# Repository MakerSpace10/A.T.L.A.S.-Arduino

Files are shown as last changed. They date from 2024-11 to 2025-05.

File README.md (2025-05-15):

# A.T.L.A.S.-Arduino

The acronym 'A.T.L.A.S.' stands for 'Aboriginal Traversal Land Analysis System'. I named it this because it is my first real robotics project and it can traverse the land around it.

The goal of this project is to create a two-wheeled, self-balancing robot, that can be remote controlled by a Wii Nunckuck. This project was originally intended for a [competition](https://robogames.net/rules/balancer.php) in the [Robo Games](https://robogames.net/index.php) event, in California. The two main focuses of the project are: the Wii Nunchuck "adapter", and the robot itself. Here is a deep dive into the build process/code. The code examples can be found in their entirety in the folder above.

## Remote

### Library
The Wii Nunchuck uses the I2C protocal to comunicate with the Wii Remote, the Arduino boards also use this to communicate with sensors. If you look on the inside of the Nunchuck plug, the slot there is conviniently the same thickness as a common circut board. This will allow for the use of a [Wii Nunckuck Adapter](https://www.amazon.com/FainWan-Compatible-WiiChuck-Nunchuck-Ar-duino/dp/B09LM69T4V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). For wiring ONLY, follow this [guide](https://www.youtube.com/watch?v=vhJRR_7m6z4). As for programming, user [madhephaestus](https://github.com/madhephaestus) has done the hard part and created a library to communicate with the Wii Nunchuck. This library is called [Wiichuck](https://github.com/madhephaestus/WiiChuck) and has been vetted by Arduino themselves. Please note: the Wii Nunchuck has a joystick, two buttons, a gyroscope/accelerometer; I will only use the joystick. If you want to use the other values, please look through the library documentation.

After adding the library to your IDE, you can get started. Start by using a global variable:
```
Accessory nunchuck1;
```
This is an object that will represent the Nunckuck.

```
nunchuck1.begin(); // Initialize the WiiChuck object
nunchuck1.type = NUNCHUCK;
```
The first line initializes the object. Now it is the Nunckuck object. The library can be used for any Wii accessories. The second line is there to prevent any errors that the library may have regognizing the accessory. 

```
nunchuck1.readData();
Serial.print("X: ");
Serial.println(nunchuck1.getJoyX());
Serial.print("Y: ");
Serial.println(nunchuck1.getJoyY());
```
This takes in the updated values comming from the Wii Nunchuck and prints them to the Serial Monitor. All the functions are very intuitive and self explanitory. The rest of the code is in the "Code/WiichuckStarter" folder.

### Transceiver
A transceiver is a modual that can send and recive data. For this project I used the NRF24L01 base modual. This has a range of about 100 meters. In freedom units that's over 300 feet. When adding it to the project, follow [How to Mechatronics](https://howtomechatronics.com/tutorials/arduino/arduino-wireless-communication-nrf24l01-tutorial/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,-Let's%20take%20a&text=It%20uses%20the%202.4%20GHz,2.4%20%E2%80%93%202.5GHz%20ISM%20band) guide. They go into much further detail than I care to do. When wiring, include a 10-100 uF capasitor. This will prevent any power supply noise and any associated issues.

```
RF24 radio(7, 8); // CE, CSN
```
Setting the radio's pins to specific ones on the board.

```
const byte address[6] = "00001";
```
This is the address of the transceiver. The transceiver will only send to / recive from this address. The prefix "const" just means it can't change.

```
struct Data_Package {
  int joyX = 0;
  int joyY = 0;
};
```
This is the data package that is sent over the transceiver. Think of it like any other package: it has contence and will only be sent to one address. The largest it can be is 32 bytes, this example is 4 bytes, so we're safe.

After the code previosly mentioned, it becomes very different based on what task it's doing. See the [How to Mechatronics](https://howtomechatronics.com/tutorials/arduino/arduino-wireless-communication-nrf24l01-tutorial/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,-Let's%20take%20a&text=It%20uses%20the%202.4%20GHz,2.4%20%E2%80%93%202.5GHz%20ISM%20band) guide for the full explanation.

Both the transceiver and the Nunchuck operate with 3.3v. The Arduino Uno only has one 3.3v pin; plugging both into the same pin would draw too much current (mA). This could damage the board. I found it's better to use the 5v pin and add a voltage regulator before adding the pins for the transeciver and the Nunchuck. This brings the voltage to the needed 3.3v while also making more current (mA) avalible to the curcit. When using a breadboard, select three rows (one for GND, one for input VCC, and one for output VCC). The regulator will connect to all three. Follow it [guide](https://www.youtube.com/watch?v=zMA1PjUn87g) for a visual representation. Remember to add the 10 uF capasitor after the regulator and before the transeciver/Nunchuck. The rest of the code is in the "Code/FinalRemote" and "Code/Receiver" folders.

Don't worry if the cover doesn't sit nicely on the housing. The amount of wires need to make the project function will push the cover off.

When pluging the Nunchuck into the 'adapter', be sure to have the 'dip' of the plug facing up. If an off-brand Nunchuck is used, there may not be proper contanct. I suggest sticking to the ones sold by Nintendo directly. 

## Robot

### Gyroscope
If the robot is going to balace on two wheels, it needs to detect when it is tilting/falling. That is the job of the GY-521 modual. This also uses the I2C protocall to comunicate. We will use the Wire library to do so, because we don't need to do anything fancy. The MPU6050 library will allow for easy reading of the data. 

```
MPU6050 mpu;
```
This creates the object that the code can refer to anywhere.

```
int16_t ax, ay, az;
int16_t gx, gy, gz;
```
This creates a name for all the values provided by the GY-521.

Start the I2C communication with 
```
Wire.begin();
```
and initialize the mpu object with 
```
mpu.initialize();
```

It's always good to test for proper conection. The following detects (and tells you) if everything is properly conected:
```
if (mpu.testConnection()) {
    Serial.println("MPU6050 connection successful");
  } else {
    Serial.println("MPU6050 connection failed");
  }
```

Assign the values to their variable names
```
mpu.getAcceleration(&ax, &ay, &az);
mpu.getRotation(&gx, &gy, &gz);
```

Now print them to the Serial moitor for user readability:
```
// Print accelerometer values (in raw units)
Serial.print("Accelerometer X: ");
Serial.print(ax);
Serial.print(" Y: ");
Serial.print(ay);
Serial.print(" Z: ");
Serial.println(az);

// Print gyroscope values (in raw units)
Serial.print("Gyroscope X: ");
Serial.print(gx);
Serial.print(" Y: ");
Serial.print(gy);
Serial.print(" Z: ");
Serial.println(gz);
```

This explains how to get the raw, non-human readable values of the gyroscope. However to avoid too much complex math, and not confuse ourselves in the process, we stick to the accelerometer values. The number used calculates the value for normal gravity:
```
float Ax = (float)ax / 16384.0;
float Ay = (float)ay / 16384.0;
float Az = (float)az / 16384.0;
```

Calculate the pitch angle:
```
float pitch = atan2(Ax, sqrt(Ay * Ay + Az * Az)) * 180.0 / PI;
```

For sanity's sake, I added a sensor fillter. This will take the average of a specified number of gyroscope values, and prevent the robot from having (its equvilent to) a seizure.
```
int FILTER_SIZE = 10 // Number of readings to average
double pitchReadings[FILTER_SIZE]; // Array to store the last N readings
int currentIndex = 0; // Current index for storing readings
double pitchFiltered = 0; // The filtered pitch value
```

and the filter array to be all 0's:
```
for (int i = 0; i < FILTER_SIZE; i++) {
  pitchReadings[i] = 0;
}
```

The rest of the filter is straight forward:
```
// Remove the oldest reading and add the new pitch reading
pitchReadings[currentIndex] = pitch;
  
// Move to the next index (wrap around if necessary)
currentIndex = (currentIndex + 1) % FILTER_SIZE;

// Calculate the average of the last N readings
pitchFiltered = 0;
for (int i = 0; i < FILTER_SIZE; i++) {
  pitchFiltered += pitchReadings[i];
}
pitchFiltered /= FILTER_SIZE;
// Reduces sudden jumps in sensor readings caused by noise, leading to smoother control of the system.
// This helps the PID controller perform more effectively since it's operating on a less noisy signal.
// In dynamic systems, a filter helps the controller focus on significant changes in the input rather than reacting to minor fluctuations.
```

The rest of the code is in the "Code/Gyro" folder.

### Stepper Motor
In order for the robot to corecct its balance, and move in general: I'm using two NEMA 17 stepper motors. They will provied a good balace of acuracy and weight (so the robot does't fall over). For wiring, follow this [guide](https://www.youtube.com/watch?v=7spK_BkMJys). The video is good for side by side walkthroughs, the [website](https://howtomechatronics.com/tutorials/arduino/stepper-motors-and-arduino-the-ultimate-guide/) is better for self-pacing. Make sure: everything is wired correctly, the driver is set correctly, and that the battery is charged/not weak.

If you're using the wires provided by the seller to connect the motor to the driver, the wire to pin translation is: Black to 1A, Green to 1B, Red to 2A, and Blue to 2B.

I will be using the AccelStepper library to control both motors. Lets start with one:

Define the pins that control the stepper motor:
```
#define stepPin 2
#define dirPin 3
```

Create a stepper motor object (We will refer to this when calling the functions):
```
AccelStepper stepper(AccelStepper::DRIVER, stepPin, dirPin);
```

Set both the max speed and the acceleration of the motor:
```
stepper.setMaxSpeed(1000); // Max speed (steps per second)
stepper.setAcceleration(50); // Acceleration (steps per second^2)
```

You could set the starting position (This is so you can move it by position, instead of times rotated): 
```
stepper.setCurrentPosition(0);
```

Rotate the wheel to position 800:
```
stepper.moveTo(800);
// Run the motor until it reaches the target position
while (stepper.distanceToGo() != 0) {
  stepper.run(); // Keep the motor moving towards the target
}
```

AccelStepper allows for changing the direction to be easy, just use a negative sign (-).
```
stepper.moveTo(-800);
```

The code listed above allows for movement by absolute position, not by steps. Instead the following function is used:
```
stepper.move(800);
```
This will rotate the stepper 4 times (800 steps / 200 steps per rotation = 4 rotations), no matter what position it is at. With this method, the idea of using a negative sign still works the same way. The only difference is now the code does not need to check if the stepper has rotated enough.

However, for this project, I need the speed of the wheels to change, no the steps. In stead I use 
```
stepper.setSpeed(800);
```
The idea of the negative sign changing directions still works here. At the beginning of the loop, add
```
stepperR.runSpeed();
```
as the steppers need to run continuously.

The rest of the code (and use of the two different functions) is in the "Code/Stepper" folder.

### Balancing
For the robot to balance on it's own: it needs a special controller called a P.I.D. Controller. P.I.D. stands for Proportional-Integral-Derivative. There is a lot of complicated math to it. To put it Layman's terms: it takes the angle we are leaning at, compares it to the angle we want to be at (0 degrees for straight up), to find out how drasticly we need to move to get there and not fall over. Use these guides: [Hackster.io](https://www.hackster.io/marketingmanagerofdattabanur/arduino-self-balancing-robot-e23f9c), [What is a P.I.D. Control](https://www.youtube.com/watch?v=wkfEZmsQqiA), [PID Control - A brief introduction](https://www.youtube.com/watch?v=UR0hOmjaHp0), and the PID Explaination PDF to understand the concepts better. Each robot will be built differently, so the P.I.D. variables will need to be tweaked. The general ideas will always be present.

The P.I.D. library in this example is the [PID_v1](https://github.com/br3ttb/Arduino-PID-Library/tree/master). I found it to be simple and easy to use. Please note that you need to manually download the library from the repository, and upload it to the Arduino IDE. 

The import statment needs to look like this:
```
#include <PID_v1.h>
```

Now set all variables the P.I.D. controller uses:
```
double Setpoint, Input, Output;
double Kp = 2.0, Ki = 5.0, Kd = 1.0;
PID myPID(&Input, &Output, &Setpoint, Kp, Ki, Kd, DIRECT);
```

Set the P.I.D. controller values:
```
Setpoint = 0; // Target angle (e.g., 0 degrees pitch)
myPID.SetMode(AUTOMATIC);
```

Outside both loops, to insure consistancy with the P.I.D., I added 
```
unsigned long lastPIDTime = 0;
const unsigned long pidInterval = 10; // PID update interval in ms
```
This controlls how often the controller updates. 

With this we can set the input for the P.I.D. controller to the output of the sensor filter:
```
// Set the input value for the PID control (filtered sensor data)
Input = -1 * abs(pitchFiltered);
```
The controller doesn't seem to respond well with positive values, so I just made them all negative

However: there mayby some margin of error (with the electronics or the way the robot was built), the angle might be off slightly.
To fix this: once the robot is built, stand it to be as straight up as possible. Take the angle that appears after filtering and add/subtract as needed.
Just the number before the decimal point will do. Ex.: if the robot is standing straight up and the angle is -3:
```
pitchFiltered += 3;
```
This is needed before use anywhere else. The line before setting the value of "Input" is ideal.

With that all set, we can run the P.I.D. controller:
```
myPID.Compute();
```
It's as simple as that. This will automaticly set the value of 'Output', which will be used to change the stepper motor behavior.
When it comes to controlling the stepper motors with "Output", the value does not translate perfectly to motor steps, so we multiply.

This way the stepper motors will move the appropiate amount of steps to remain upright. It will move the appropiate direction based of of the direction of the pitch.

As a neat feature (for sanity's sake), it's good to stop the robot from moving if it leans too much. After the pitch passes a certain threshold, it cannot prevent itself from falling over. If it does, the wheels will keep spining, continuing to move the robot. To avoid this, "Input" is set inside a if statment:
```
// A max of 15 degree tilt
if(abs(pitchFiltered) < 15){
  Input = -1 * abs(pitchFiltered);
  myPID.Compute();

  stepSpeed = (int)(Output * 10);
  if(pitchFiltered > 0){
    stepper.setSpeed(stepSpeed);
  }else{
    stepper.setSpeed(-stepSpeed);
  }
}else{
  Serial.println("Please reset robot position.");
  stepper.setSpeed(0);
}
```

For debugging (optional):
```
Serial.print("Pitch: ");
Serial.print(pitchFiltered);
Serial.print("\tOutput: ");
Serial.print(Output);
Serial.print("\tError: ");
Serial.print(Setpoint - pitchFiltered);
Serial.print("\tSpeed: ");
Serial.println(stepSpeed);
```

Finnally, the reciver and the balancer code combine. The balancer code will take priority, so the robot doesn't fall over.

### Remote Commands
The Nunchuck values will not be (0,0) at the center. All values will vary slightly, reguardless of previous recorded positions. So to overcome this, create a board representing the positions of the joy stick on the Nunchuck, and note the values. I decided to constrain the values of 'x' and 'y' for later use:
```
  //                              Left, Right
  int x = (int)constrain(data.joyX, 30, 225);
  //                              Back, Forth
  int y = (int)constrain(data.joyY, 40, 230);
```

To prevent the robot from moving when the joy stick is in the center, I created the controls to be around a range of values. This creates a "hole" of values, to which the robot will not respond to. Please note that these are the values I got and guessed; it will be different for you. The following is a rough idea on interpreting the Nunchuck data:
```
//Left then Right
int turnSpeed;
if(x <= 125){
  turnSpeed = (int)map(x, 30, 125, 5, 50);
  stepperR.setSpeed(turnSpeed);
  stepperL.setSpeed(turnSpeed);
}else if(x >= 135){
  turnSpeed = (int)map(x, 135, 230, 5, 50);
  stepperR.setSpeed(-turnSpeed);
  stepperL.setSpeed(-turnSpeed);
}
Serial.print("\t X speed: ");
Serial.print(turnSpeed);
//Back then Forward
int linSpeed;
if(y <= 135){ 
  linSpeed = (int)map(y, 40, 135, 5, 100);
  stepperR.setSpeed(-linSpeed);
  stepperL.setSpeed(linSpeed);
}else if(y >= 145){
  linSpeed = (int)map(y, 145, 225, 5, 100);
  stepperR.setSpeed(linSpeed);
  stepperL.setSpeed(-linSpeed);
}
Serial.print("\t Y speed: ");
Serial.println(linSpeed);
```

Turning is the most unstable, so it will be slower comparded to forward and back. To turn properly, the motors need to move in opposite directions; because they face the opposite way physically, we give them the same command. Moving back/forth is straight-forward.

Warning: before using any of the code mentioned abouve, remove any and all delays and make sure all values match YOUR setup, or the code will note work the way it should. 

Happy Trails!

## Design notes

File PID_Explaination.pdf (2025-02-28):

# PID Controller

PID stands for Proportional-Integral-Derivative, and it’s a type of control algorithm used to help systems reach a desired goal or setpoint (like keeping the temperature of a room constant).
Here’s a simple breakdown of the three components of a PID controller:
1. Proportional (P):
This part looks at the current error, which is how far the system is from the target value. The proportional part tries to correct the error by applying a correction that’s proportional to the size of the error.
Example: If your room is 5°C cooler than desired, the system will apply a correction that's proportional to that error (say, 5 times some constant).
2. Integral (I):
This part looks at the accumulated error over time. If there’s been a small error for a long time, the integral part will work to correct it by adding up all the past errors. This helps eliminate any steady-state errors that the proportional part might miss.
Example: If the room temperature has been slightly too low for a long time, the integral part will push harder to correct this over time.
3. Derivative (D):
This part looks at the rate of change of the error. It anticipates how fast the error is changing and tries to adjust the correction to prevent overshooting or instability.

Example: If the temperature is rapidly increasing towards the target, the derivative part will slow down the heating to avoid going past the target temperature.

### Putting it all together:

A PID controller adjusts the system's output by combining the three components: The Proportional part responds to how big the error is right now.

PID Controller | 1

The Integral part compensates for past errors.

The Derivative part anticipates future changes.
By balancing these three components, the PID controller tries to minimize the error and make the system as stable as possible.

When tuning a PID controller, it’s helpful to understand how each of the three constants (Kp, Ki, and Kd) affects the system behavior. Here's how you can figure out which value to adjust:

### 1. Proportional (Kp) – Adjusting for the Size of the Error

The proportional term determines how much correction is applied based on the current error (the difference between your setpoint and the current value).

If Kp is too high:
The system will respond quickly, but it might overshoot the setpoint, causing the system to oscillate back and forth around the target.

It might cause the system to be "too aggressive," trying to correct too much.

If Kp is too low:
The system will respond too slowly or may never reach the setpoint. It won't be able to overcome the error, and the response will be sluggish.

To adjust Kp:
Start with a small value and increase it gradually.

The goal is to make the system respond quickly to error, but without causing too much overshoot or oscillation.

### 2. Integral (Ki) – Adjusting for Accumulated Error

The integral term accounts for the sum of past errors. This helps the system eliminate steady-state errors (errors that don’t go away with just the proportional term, like if the system stays a little off target over time).
If Ki is too high:

The system might "overcompensate" by continually adding up past errors and trying to correct them too much. This can lead to oscillation or instability.

If Ki is too low:
The system might not be able to eliminate small errors over time, and it might leave a persistent error even after the system seems stable.

To adjust Ki:
Increase Ki slightly if the system is unable to reach the setpoint or if there’s a persistent small error over time.

Reduce Ki if the system becomes unstable or oscillates after reaching the setpoint.

### 3. Derivative (Kd) – Adjusting for Rate of Change

The derivative term looks at how fast the error is changing. It tries to anticipate how the error will evolve and dampens any sudden changes to prevent overshooting.
If Kd is too high:

The system might become overly sensitive to small fluctuations in error, making it too slow or too "nervous," correcting even small changes too much.
If Kd is too low:

The system might overshoot and oscillate because it’s not responding to rapid changes in the error.

To adjust Kd:
Increase Kd if the system is overshooting (going past the setpoint) or if it’s oscillating.

If the system is responding too slowly, try lowering Kd to reduce unnecessary dampening.

### A Practical Process for Tuning:

1. Start with Kp first:

Set Ki and Kd to zero initially.
Gradually increase Kp until the system starts to respond to the error. Look for a value where the system reacts quickly without oscillating too much.
2. Add Ki:
Once Kp is set, start increasing Ki gradually.

If there’s a persistent error (like the system never quite reaches the setpoint), increase Ki to eliminate it.

Be careful not to set Ki too high, as it can cause instability.
3. Add Kd:

Finally, adjust Kd to reduce oscillations and overshooting.
If the system is overshooting or oscillating, increase Kd to help "dampen" the response.

### A Tuning Strategy to Try:

There’s a common strategy called the Ziegler-Nichols Method that can help guide you through the process of tuning PID constants:

1. Set Ki and Kd to 0.
2. Increase Kp until the system starts oscillating.
3. Record the value of Kp at which the system starts oscillating. This is called the ultimate gain (Ku).
4. Measure the period of oscillation, which is the time it takes for one full cycle of oscillation (the ultimate period, Pu).
5. Use the following rules to calculate your PID values:

Proportional (Kp):
Kp=0.6×KuKp = 0.6 \times Ku
Integral (Ki):
Ki=2×Kp/PuKi = 2 \times Kp / Pu

Derivative (Kd):
Kd=Kp×Pu/8Kd = Kp \times Pu / 8

After applying these values, fine-tune them manually for the best performance.

### Other Tips:

Fine-tuning is key. You’ll likely need to tweak the values slightly after using the Ziegler-Nichols method or your initial guesswork.
Monitor system behavior carefully (e.g., through serial prints or graphs) to make sure you're not causing instability.

For very slow systems (like temperature control), a high Ki value is often useful, while for fast-reacting systems (like motors or robots), you might rely more on the proportional and derivative components.

### Example Process:

Let's say you’re controlling a heater's temperature:
1. Set Ki and Kd to 0.
2. Slowly increase Kp until you notice the temperature starts to increase faster but doesn’t oscillate too wildly.
3. If the temperature overshoots and oscillates, add a small Kd to dampen the response.
4. If there's still a persistent low error, slowly increase Ki to help the system get to the target temperature more precisely.

By adjusting these three constants gradually, you can find a balance where the system is stable, responsive, and accurate.

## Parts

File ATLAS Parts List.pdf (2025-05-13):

Remote:
Part Name: | Price - Units: Some links:
Wii Nunchuck | | Make sure that the seller is Nintendo
Arduino Nunchuck Adapter | $13 for 5 | https://www.amazon.com/FainWan-Compatible-WiiChuck-Nunchuck-Ar-duino/dp/B09LM69T4V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 (https://www.amazon.com/FainWan-Compatible-WiiChuck-Nunchuck-Ar-duino/dp/B09LM69T4V?s=videogames)

Arduino Uno/nano
Battery “Pack” | A 9v battery should work fine.
NRF24L01 | $8 -4 | https://www.amazon.com/HiLetgo-NRF24L01-Wireless-Transceiver-Module/dp/B00LX47OCY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 A5HF046HN5ZZYK&psc=1 (https://www.amazon.com/HiLetgo-NRF24L01-Wireless-Transceiver-Module/dp/B00LX47OCY)
10 uF Capacitor | need 2
3.3v Voltage
regulator
| $8 - 20 | https://www.amazon.com/Ferwooh-AMS1117-3-3-4-5V- 7V-AMS1117-3-3V-Converter/dp/B0D17N8WWJ/ref=sr _1_5?crid=26I050O33AR7Y&dib=eyJ2IjoiMSJ9.yYoap YX0zQQVL-GhrZ4MBW5fwuoTvOJPqwwwicoQy3tW pLhC7DvnTZpdporOD4W-J1sqX_HDa0aT5zoH6hzlbvg uVB_GJ-Lvw-RSH27blJZRefK2SKfLUocBsBrzznpvsV q9Ug12vn2sIzaQEEpmxCYL1oHuYf2rWTOw5LPDTp M2epp-RwoUdLc1iKdejKdiajcoiga38SGo1UPzXbp40L ogGkZJbVWgB4BXRnFWGFaDx5gF0UC3OC2LrWiB KNW-Z4qeOSYyR6TuqTqDQt9KvmWsQcyg20MPVpL zhIbBigg.XxFXhx4V4o8Xa2L5BvKZuC0R84E-zATMQ oEUQHv6Z14&dib_tag=se&keywords=5v+to+3.3v+volt age+divider&qid=1747142222&s=industrial&sprefix=5v +to+3.3v+voltage+divider%2Cindustrial%2C57&sr=1-5 (https://www.amazon.com/Ferwooh-AMS1117-3-3-4-5V-7V-AMS1117-3-3V-Converter/dp/B0D17N8WWJ?s=industrial)

Robot:
Part Name: | Price: | Some Links:

Arduino Uno/Nano
2 Stepper Motors | $8-1 or $40 - 5 | https://www.amazon.com/Usongshine-Nema17-Stepper-17HS4401S-Printer/dp/B0787BQ4WH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 (https://www.amazon.com/Usongshine-Nema17-Stepper-17HS4401S-Printer/dp/B0787BQ4WH)

| | q7sbz&content-id=amzn1.sym.a089f039-4dde-401a-9041 -8b534ae99e65&pf_rd_p=a089f039-4dde-401a-9041-8b5 34ae99e65&pf_rd_r=B8Z8AJ2SPGXADPE419P9&pd_r d_wg=vq1IF&pd_rd_r=93860624-13ea-4a1d-8257-0d5a9 e81c6ce&pd_rd_i=B07KW7F3P9&th=1 (https://www.amazon.com/Usongshine-Nema17-Stepper-17HS4401S-Printer/dp/B0787BQ4WH)
2 Stepper Motor Drivers | $10-5 | https://www.amazon.com/HiLetgo-Stepstick-Stepper-Printer-Compatible/dp/B07BND65C8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 07BND65C8&psc=1 (https://www.amazon.com/HiLetgo-Stepstick-Stepper-Printer-Compatible/dp/B07BND65C8)
Stepper Motor Mounting Brackets | $10 - 2 | https://www.amazon.com/weideer-Stepper-Mounting-Bracket-K-029-42/dp/B09372B2D1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 09372B2D1&th=1 (https://www.amazon.com/weideer-Stepper-Mounting-Bracket-K-029-42/dp/B09372B2D1)
GY-521 Accelerometer/Gyro scope | $8.50-3 | https://www.amazon.com/FORIOT-Accelerometer-MPU-6050-Compatible-Converter/dp/B0CDL8DVZ7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 (https://www.amazon.com/FORIOT-Accelerometer-MPU-6050-Compatible-Converter/dp/B0CDL8DVZ7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)
Transceiver | Taken Care of.
Battery Pack | | Find one that the drivers can handle.
100 uF Capacitor | | One for each driver.

### 2 non-slip wheels

and mounting hub

$13-2
and
$14-2

https://www.amazon.com/90-10mm-Black-Robot-Wheels/dp/B00T3MQG7M/ref=sr_1_53?dib=eyJ2IjoiMSJ9.J3dg x8P762UnXWORtlwJYXmVniWD9I0SaMzqaugb5KLU BAPJapvnl7OtTUPSE1LhI3VgLKNvX7wmI0-zaRnMgn GDNnxRQ7D8U_xinsZm4ENyCvHIdXOUPfZb6aoGjUf 6Wge3jFfUSyg81EokhgKNOsa4FpTjyiPosZVvxWJQ09 8sSDo7SOz8R39l0S_avcjpI-lWVV7BhM35hT-ujsWoa-U5dzt3hWNCo6FdP1j1FB1Omf6be6oA0wI54QWy7BL kd_qfB-8SnS2gCqVgXwxTvzH9Q0SlkLZ8sBS4QR2vu 7Q.bxDL5dnFUvPnqkcdF5KDHgBz9bM-7mfJWLQtIcji xac&dib_tag=se&keywords=arduino+wheels&qid=17295 31853&sr=8-53 (https://www.amazon.com/90-10mm-Black-Robot-Wheels/dp/B00T3MQG7M)
and
https://www.amazon.com/Pololu-Universal-Aluminum-MOUNTING-Shaft/dp/B00B887FX8/ref=pd_bxgy_thbs_d_ (https://www.amazon.com/Pololu-Universal-Aluminum-MOUNTING-Shaft/dp/B00B887FX8)

sccl_1/143-0492769-7445039?pd_rd_w=UnJN6&content -id=amzn1.sym.f7fa8b58-6436-47b8-8741-9e90c231669e &pf_rd_p=f7fa8b58-6436-47b8-8741-9e90c231669e&pf _rd_r=3ZPERPRNYQMZRZDAVVQ6&pd_rd_wg=P97 Bp&pd_rd_r=4b8d5db8-37d0-431c-8c29-d2db8ca5031f &pd_rd_i=B00B887FX8&psc=1 (https://www.amazon.com/Pololu-Universal-Aluminum-MOUNTING-Shaft/dp/B00B887FX8)
5mm bars for the
frame
$12-10 | https://www.amazon.com/VictorsHome-Stainless-Crafts- Helicopter-Airplane/dp/B0962X6J95/ref=sr_1_3?crid=3 OTEF9LOTIY3W&dib=eyJ2IjoiMSJ9.ch840XSb-mjD1k YPgweX40GilWj2algdChaO4agcDgWod5fDWyxYlj7SJ 7pQTUngiGWZeF5di4CgiKJmkF2rFuLfFcfKUWopdnG PJ7ohA3ESe980wfDbDK0uust2g1Pjsytb8Qdp6K2e_bnG B2kssx6cMU53DdcFPJF2QCMRpFBUt84RXgI5p6D8h Ox2k8Hf-qbAbDYWbARXy8VGMJUAd2aWMq3STDc 86N3SZKQuCu4.izOUcmmDijLX7o_l7hrYsKBIXQvQ MYoteCUvzMzrgcc&dib_tag=se&keywords=5mm%2Bx %2B200mm%2Brods&qid=1727287311&sprefix=5mm %2Bx%2B200mm%2Brods%2Caps%2C58&sr=8-3&th=
| 1 (https://www.amazon.com/VictorsHome-Stainless-Crafts-Helicopter-Airplane/dp/B0962X6J95)

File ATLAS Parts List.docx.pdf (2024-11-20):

### Remote:

Part Name: | Price: | Some links:

Wii Nunchuck
Arduino Nunchuck Adapter | $13 for 5 | https://www.amazon.com/FainWan-Compatible-WiiChuck-Nunchuck-Ar-duino/dp/B09LM69T4V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 (https://www.amazon.com/FainWan-Compatible-WiiChuck-Nunchuck-Ar-duino/dp/B09LM69T4V?s=videogames)
Logic level shifter | $7.50 - 10 | https://www.amazon.com/HiLetgo-Channels-Converter-Bi-Directional-3-3V-5V/dp/B07F7W91LC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 (https://www.amazon.com/HiLetgo-Channels-Converter-Bi-Directional-3-3V-5V/dp/B07F7W91LC?s=industrial)

Arduino Uno/nano
Battery “Pack” | A 9v battery should work fine.
NRF24L01 | $8 -4 | https://www.amazon.com/HiLetgo-NRF24L01-Wireless-Transceiver-Module/dp/B00LX47OCY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 f&pf_rd_r=HR740JA5HF046HN5ZZYK&psc=1 (https://www.amazon.com/HiLetgo-NRF24L01-Wireless-Transceiver-Module/dp/B00LX47OCY)
10 uF Capacitor | need 2
3.3v Voltage regulator | need 2
3-D printed Housing

### Balancing Robot:

Part Name: | Price: | Some Links:

Arduino Uno/Nano
2 Stepper Motors | $11-1 | https://www.amazon.com/Usongshine-Nema17-Stepper-17HS4401S-Printer/dp/B0787BQ4WH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 pd_rd_i=B07KW7F3P9&th=1 (https://www.amazon.com/Usongshine-Nema17-Stepper-17HS4401S-Printer/dp/B0787BQ4WH)
2 Stepper Motor Drivers | $10-5 | https://www.amazon.com/HiLetgo-Stepstick-Stepper-Printer-Compatible/dp/B07BND65C8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 (https://www.amazon.com/HiLetgo-Stepstick-Stepper-Printer-Compatible/dp/B07BND65C8)

| | .sym.2b132e63-5dcd-4ba1-be9f-9e044543d59f&pf_rd_p= 2b132e63-5dcd-4ba1-be9f-9e044543d59f&pf_rd_r=0BF9X HJZB9Q1QV2H1FRA&pd_rd_wg=u2m9L&pd_rd_r=90a0f3 48-26f9-4319-8482-a2a2ec24d3f9&pd_rd_i=B07BND65C8 &psc=1 (https://www.amazon.com/HiLetgo-Stepstick-Stepper-Printer-Compatible/dp/B07BND65C8)
Stepper Motor Mounting Brackets | $10 - 2 | https://www.amazon.com/weideer-Stepper-Mounting-Bracket-K-029-42/dp/B09372B2D1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 th=1 (https://www.amazon.com/weideer-Stepper-Mounting-Bracket-K-029-42/dp/B09372B2D1)
GY-521 Accelerometer/Gyrosco pe | $8.50-3 | https://www.amazon.com/FORIOT-Accelerometer-MPU-6050-Compatible-Converter/dp/B0CDL8DVZ7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 (https://www.amazon.com/FORIOT-Accelerometer-MPU-6050-Compatible-Converter/dp/B0CDL8DVZ7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)
Transceiver | Taken Care of.
Battery Pack

### 2 non-slip wheels and

mounting hub

$13-2
and
$14-2

https://www.amazon.com/90-10mm-Black-Robot-Wheels/dp/B00T3MQG7M/ref=sr_1_53?dib=eyJ2IjoiMSJ9.J3dgx8P 762UnXWORtlwJYXmVniWD9I0SaMzqaugb5KLUBAPJapvnl 7OtTUPSE1LhI3VgLKNvX7wmI0-zaRnMgnGDNnxRQ7D8U_ xinsZm4ENyCvHIdXOUPfZb6aoGjUf6Wge3jFfUSyg81Eokhg KNOsa4FpTjyiPosZVvxWJQ098sSDo7SOz8R39l0S_avcjpI-l WVV7BhM35hT-ujsWoa-U5dzt3hWNCo6FdP1j1FB1Omf6b e6oA0wI54QWy7BLkd_qfB-8SnS2gCqVgXwxTvzH9Q0SlkLZ 8sBS4QR2vu7Q.bxDL5dnFUvPnqkcdF5KDHgBz9bM-7mfJW LQtIcjixac&dib_tag=se&keywords=arduino+wheels&qid=1 729531853&sr=8-53 (https://www.amazon.com/90-10mm-Black-Robot-Wheels/dp/B00T3MQG7M)
and
https://www.amazon.com/Pololu-Universal-Aluminum-MOUNTING-Shaft/dp/B00B887FX8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 887FX8&psc=1 (https://www.amazon.com/Pololu-Universal-Aluminum-MOUNTING-Shaft/dp/B00B887FX8)
Frame | $12-10 | https://www.amazon.com/VictorsHome-Stainless-Crafts-H elicopter-Airplane/dp/B0962X6J95/ref=sr_1_3?crid=3OTE F9LOTIY3W&dib=eyJ2IjoiMSJ9.ch840XSb-mjD1kYPgweX40 GilWj2algdChaO4agcDgWod5fDWyxYlj7SJ7pQTUngiGWZe F5di4CgiKJmkF2rFuLfFcfKUWopdnGPJ7ohA3ESe980wfDbD K0uust2g1Pjsytb8Qdp6K2e_bnGB2kssx6cMU53DdcFPJF2Q CMRpFBUt84RXgI5p6D8hOx2k8Hf-qbAbDYWbARXy8VGMJ (https://www.amazon.com/VictorsHome-Stainless-Crafts-Helicopter-Airplane/dp/B0962X6J95)

UAd2aWMq3STDc86N3SZKQuCu4.izOUcmmDijLX7o_l7hrY sKBIXQvQMYoteCUvzMzrgcc&dib_tag=se&keywords=5mm %2Bx%2B200mm%2Brods&qid=1727287311&sprefix=5m m%2Bx%2B200mm%2Brods%2Caps%2C58&sr=8-3&th=1 (https://www.amazon.com/VictorsHome-Stainless-Crafts-Helicopter-Airplane/dp/B0962X6J95)

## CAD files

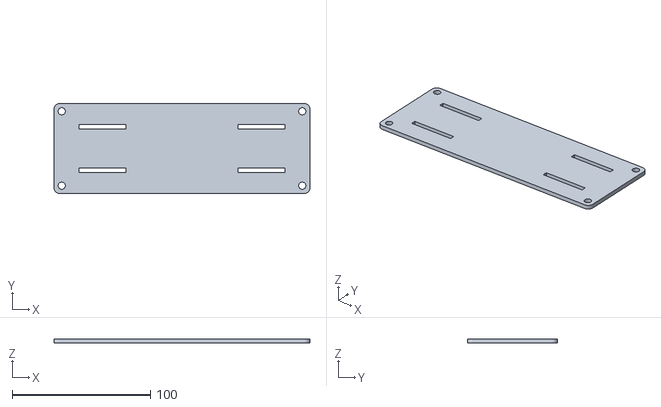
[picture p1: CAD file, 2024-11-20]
STL File/Motor Board.stl
185.0 x 65.0 x 3.00

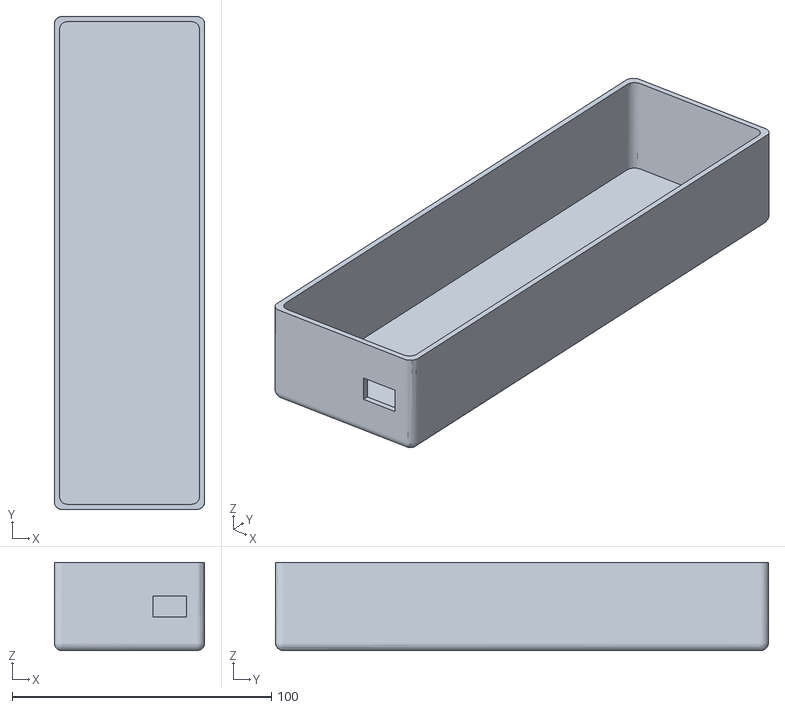
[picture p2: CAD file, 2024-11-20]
STL File/Remote Case.stl
58.0 x 190.0 x 34.0

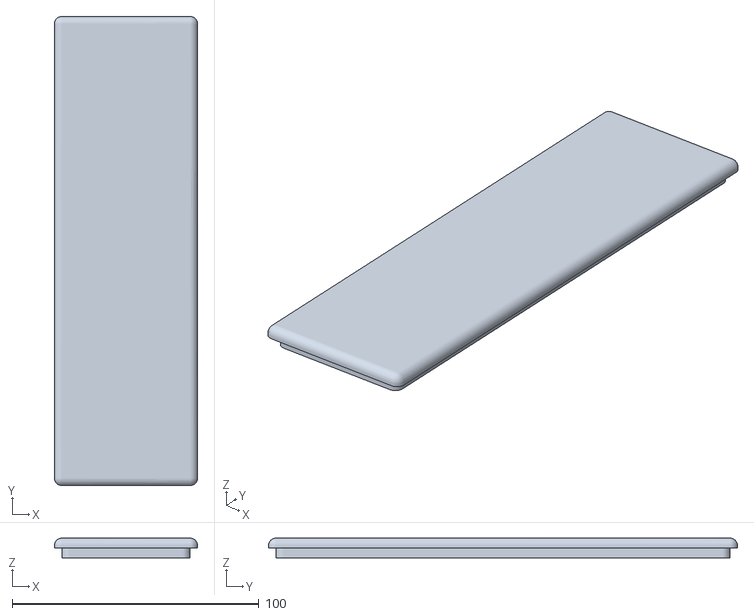
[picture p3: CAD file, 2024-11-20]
STL File/Remote Cover.stl
58.0 x 190.0 x 8.00

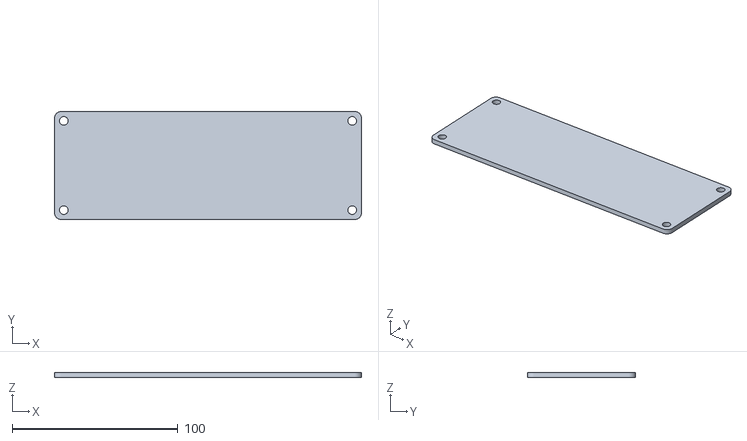
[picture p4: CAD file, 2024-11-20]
STL File/Body Board.stl
185.0 x 65.0 x 3.00

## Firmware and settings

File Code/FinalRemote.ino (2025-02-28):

#include <WiiChuck.h>
#include <SPI.h>
#include <nRF24L01.h>
#include <RF24.h>

//This is the Global Variable, you can use it anywhere in the program.
Accessory nunchuck1;

RF24 radio(7, 8); // CE pin, CSN pin

const byte address[6] = "00001";

// Max size of this struct is 32 bytes - NRF24L01 buffer limit: Do not exceed limit. Current capasity is 16 bytes.
struct Data_Package {
  int joyX = 0;
  int joyY = 0;
};

Data_Package data; // Create a variable with the above structure

void setup(){
  //Wiring
  //VCC is red
  //GND is black
  //DATA is blue
  //CLOCK is white

  //Set Baud rate for Serial Monitor
  Serial.begin(115200);
  nunchuck1.begin(); // Initialize the WiiChuck object
  nunchuck1.type = NUNCHUCK;
  
  radio.begin();
  radio.openWritingPipe(address);
  radio.stopListening();
}

void loop(){
  nunchuck1.readData();    // Read inputs and update maps
  Serial.print("X: ");
  Serial.println(nunchuck1.getJoyX());
  Serial.print("Y: ");
  Serial.println(nunchuck1.getJoyY());
  
  data.joyX = nunchuck1.getJoyX();
  data.joyY = nunchuck1.getJoyY();
  // Send the whole data from the structure to the receiver
  radio.write(&data, sizeof(Data_Package));
  
  delay(1000);
}

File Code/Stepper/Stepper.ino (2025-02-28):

#include <AccelStepper.h>

// Define motor control pins
#define stepPin 2
#define dirPin 3

// Create an instance of the AccelStepper class
// Using AccelStepper::DRIVER for stepper drivers that control step and direction pins
AccelStepper stepper(AccelStepper::DRIVER, stepPin, dirPin);

void setup() {
  // Set the maximum speed and acceleration for the motor
  stepper.setMaxSpeed(1000); // Max speed (steps per second)
  stepper.setAcceleration(500); // Acceleration (steps per second^2)

  // Optionally, set the current position
  stepper.setCurrentPosition(0); // Optional: Set starting position to 0
}

void loop() {
  // Move the motor to position 800 steps in the current direction
  stepper.moveTo(800);  // Move to position 800 (relative position)

  // Run the motor until it reaches the target position
  while (stepper.distanceToGo() != 0) {
    stepper.run(); // Keep the motor moving towards the target
  }

  // Add a delay to ensure the motor has finished moving
  delay(1000); // Wait for 1 second

  // Change direction: move to -800 steps (opposite direction)
  stepper.moveTo(-800);

  // Run the motor until it reaches the new target position
  while (stepper.distanceToGo() != 0) {
    stepper.run();
  }

  // Wait for 1 second
  delay(1000);
}

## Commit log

2024-11-20 Add STL files
    [Body Board.stl, Motor Board.stl, Remote Case.stl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]
2024-11-20 Add Reciver/Start Gyro explanation
2024-11-20 Finish Gyro explanation
2024-11-20 Add Stepper explanation
2025-02-28 Fix Stepper walkthrough
2025-03-24 Add the PID Explaination
2025-03-24 Add PID Controller code
2025-04-07 PID to Stepper Translation
2025-04-08 Gyro/PID Separation
2025-04-09 Pitch Error Fix
2025-05-13 Stepper Translation/Explaination
2025-05-13 PID Update
